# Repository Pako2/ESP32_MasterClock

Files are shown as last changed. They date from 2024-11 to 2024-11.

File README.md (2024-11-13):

# ESP32_MasterClock
## Introduction
The project addresses the solution of a simple source of polarized pulses for slave clock networks. The precise time is obtained from the internet using the NTP protocol. The heart of the device is the **ESP32-C3 SuperMini** module, which connects to the internet via WiFi. A prerequisite for the proper functioning of the device is, of course, an available WiFi signal at the deployment location.
The distribution of pulses is managed by a module equipped with two **A4950** H-bridges. The design of the module was chosen primarily to ensure easy repair in case of failure. The advantage of the dual configuration is that in the event of a failure of one bridge, it should be sufficient to rotate the module and thus use the second, previously unused bridge.
The device does not contain any adjustment elements or a display. All settings are done through a web interface. The status of the device is indicated using two LEDs. The first LED is used to indicate the status of WiFi (via a steady light or blinking). The second LED is a multi-colored (WS2812) and indicates the status of the slave clock using different colors.

Complete project documentation can be found in the [UserGuide_EN.pdf](doc/UserGuide_EN.pdf) file.

## Design of the device
The wiring diagram and circuit board were created using the Eagle design system.
### Wiring diagram
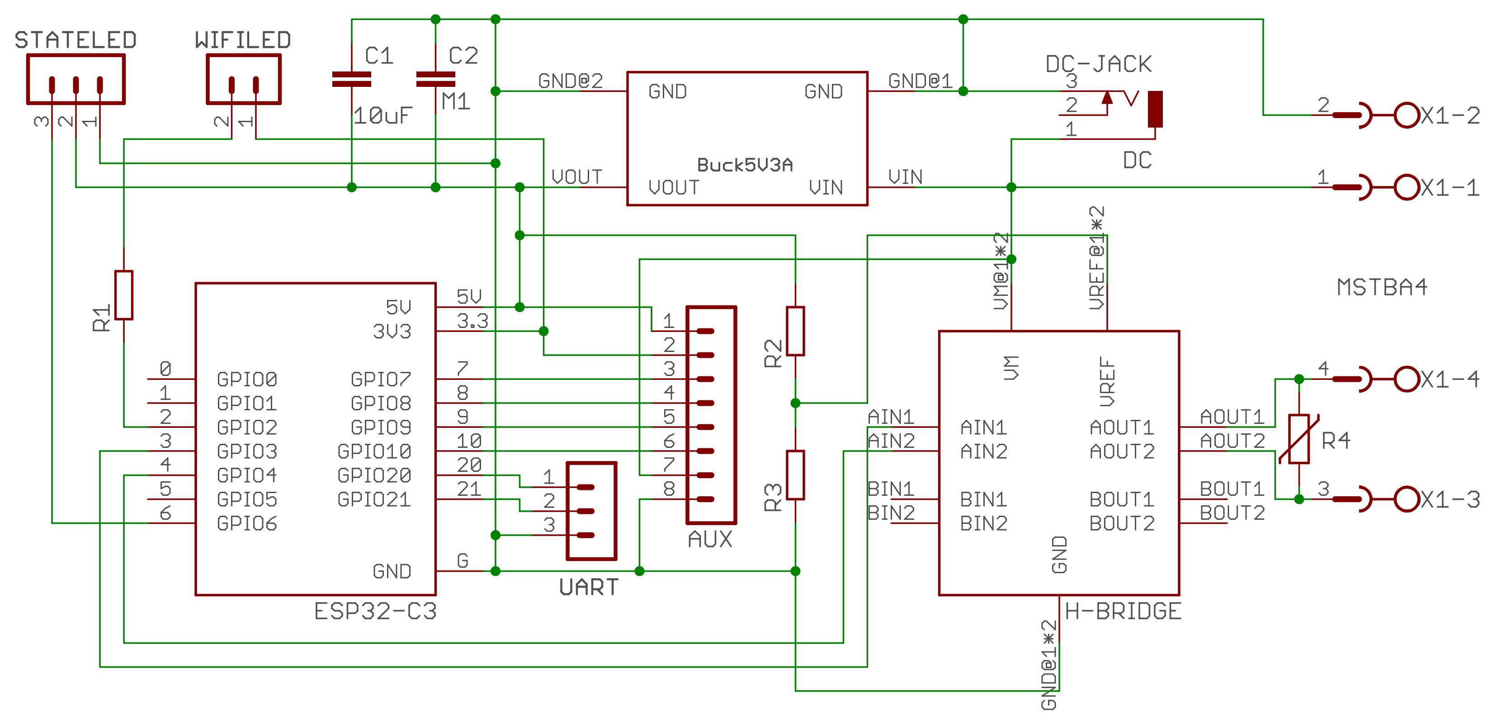
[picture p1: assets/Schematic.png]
Wiring diagram

### Printed circuit board
<p float="left">
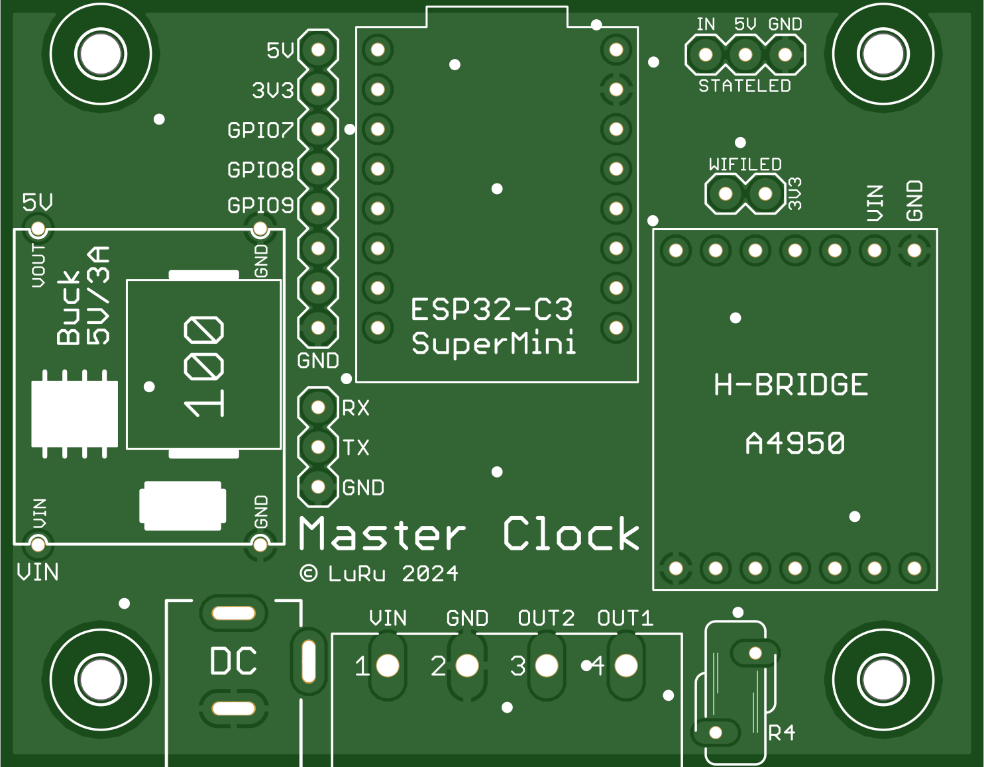
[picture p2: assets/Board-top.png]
PCB top side
  
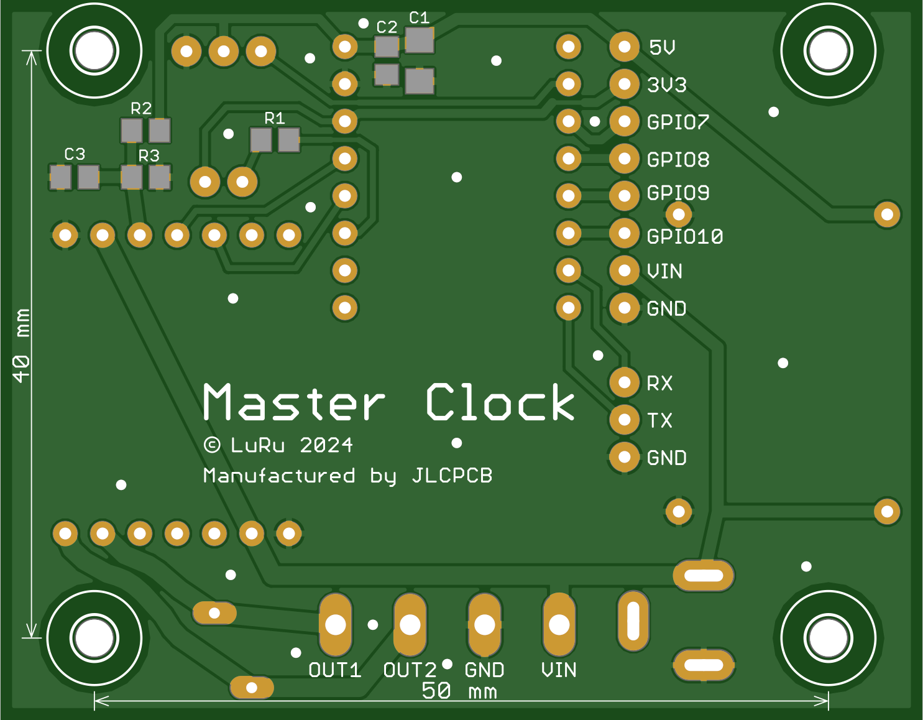
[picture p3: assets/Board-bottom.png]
PCB bottom side
   
</p>

### A box
The size of the printed circuit board and the spacing of the mounting holes were adjusted after the design so that the board fits into some - existing on the market - box. A box with dimensions of 83 x 58 x 33 mm fits perfectly.
<p float="left">
  Open box
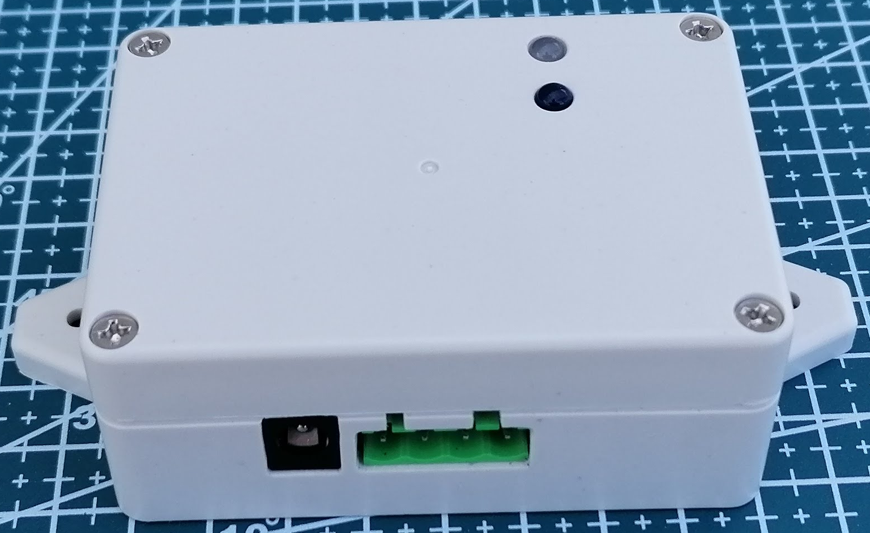
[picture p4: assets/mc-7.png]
Closed box
   
</p>

## Choice of components
Even before the design started, I was clear that one of the ESP32 chips/modules would be used in the device, and it would be one of the many existing modules to ensure easy replacement in case of failure. In the end, I chose one of the smallest modules – **ESP32-C3 SuperMini**. It is small, cheap and more than adequately equipped for the given use.
<p float="left">
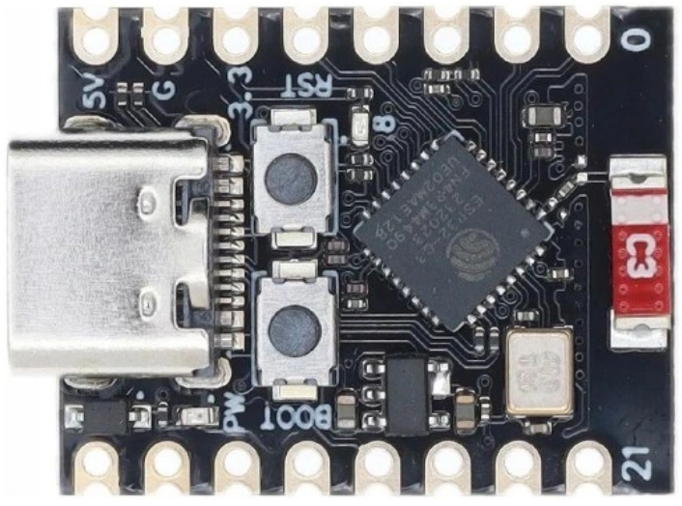
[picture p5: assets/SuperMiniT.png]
SuperMini top side
  
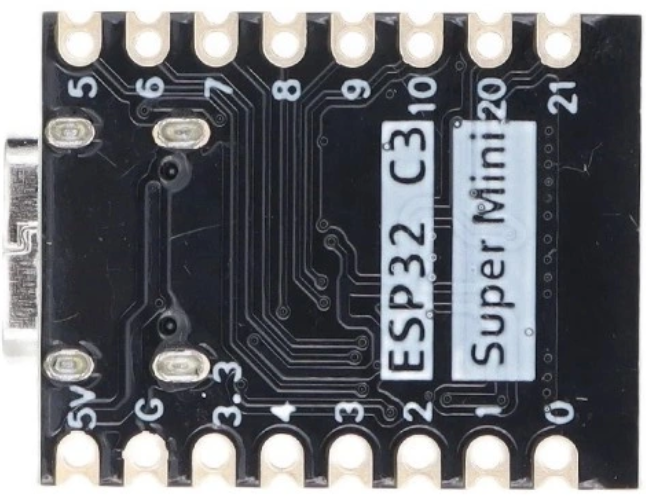
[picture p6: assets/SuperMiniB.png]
SuperMini bottom side
   
</p>

The device is powered by a voltage of 24V, which is required for the correct operation of the slave clock. However, the ESP32-C3 SuperMini module needs a voltage of 5V and therefore a suitable step-down module is used as a power source.
<p float="left">
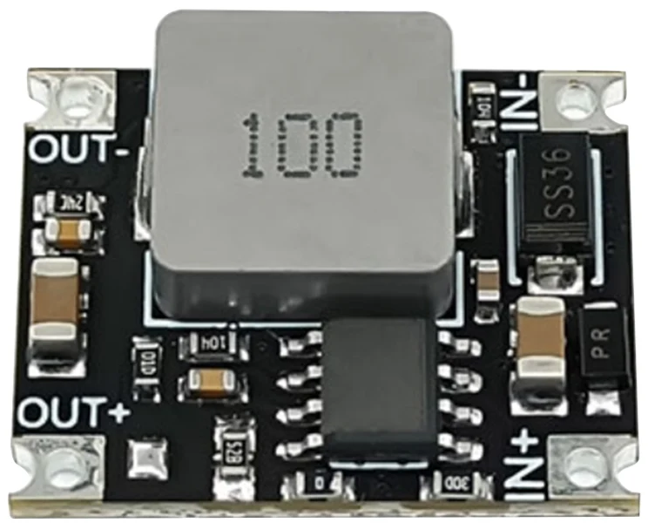
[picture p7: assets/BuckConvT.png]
Step-down converter top side
  
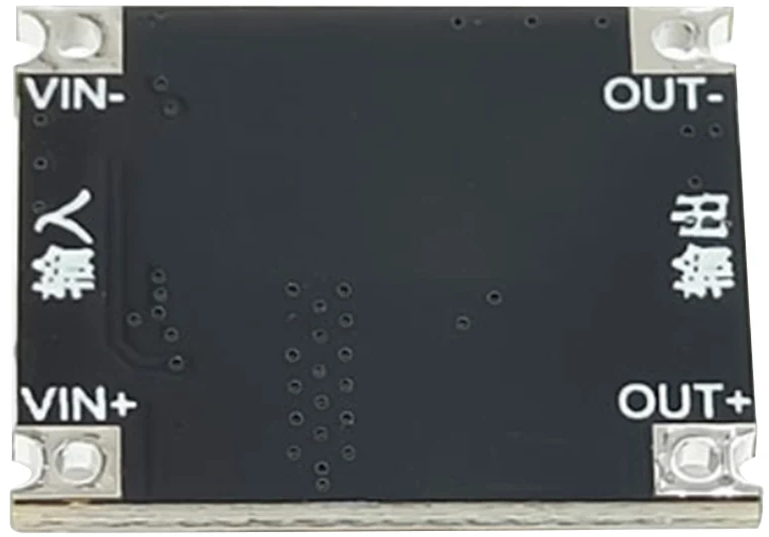
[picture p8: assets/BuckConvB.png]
PStep-down converter bottom side Step-down converter bottom side
   
</p>

The selected converter is sufficiently dimensioned both in terms of input voltage (up to 40V) and output current (up to 3A).

One of the most important components of the entire device is the H-bridge, with which polarized pulses are sent to the slave clocks. For this task, I chose the A4950 module equipped with two bridges, but only one of them is used. The second one can (due to the symmetrical design of the module) be considered as a "spare". In case of failure of the first bridge, it is enough to turn the module by 180°.
<p float="left">
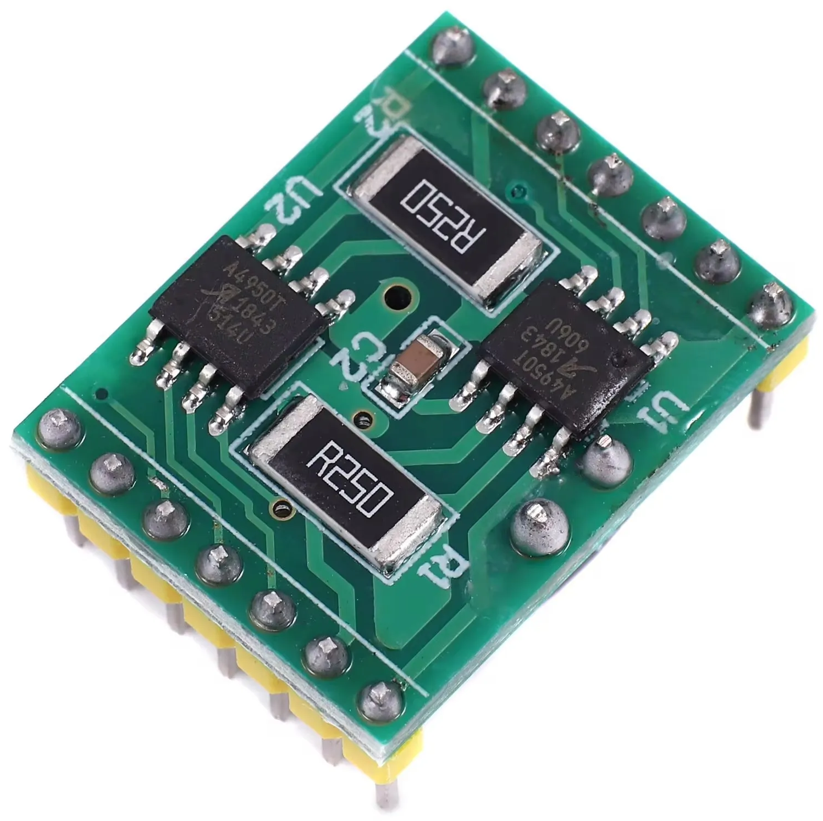
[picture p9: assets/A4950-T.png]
H-bridge top side
  
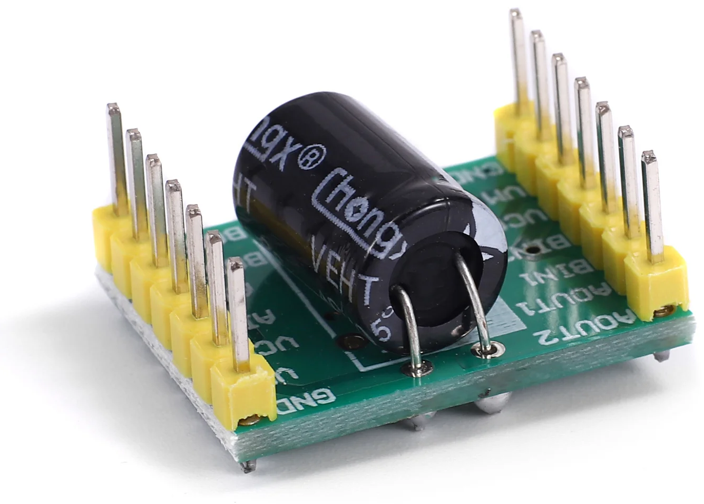
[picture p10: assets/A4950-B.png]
H-bridge bottom side
   
</p>

### Time
The device obtains the exact time from an NTP server. This requires the ESP32 to be connected to the Internet. A possible failure of Internet connectivity only affects the accuracy of the operation, and after the connection is restored, the synchronization with the NTP server (and thus also the accuracy) is automatically restored.
The transition to DST and back is done automatically (thanks to synchronization with the NTP server).
Sometimes it can happen that none of the known WiFi networks are available when the device is turned on (or restarted). Then, of course, it is not possible to synchronize the time with the NTP server. In such an extreme situation, the **Sync Browser Time to Device** button on the **NTP (Time) Settings** page will help.

### License
The code parts written by the author of the **ESP32_MasterClock** project are licensed under [MIT License](LICENSE), 3rd party libraries that are used by this project are licensed under different license schemes, please check them out as well.

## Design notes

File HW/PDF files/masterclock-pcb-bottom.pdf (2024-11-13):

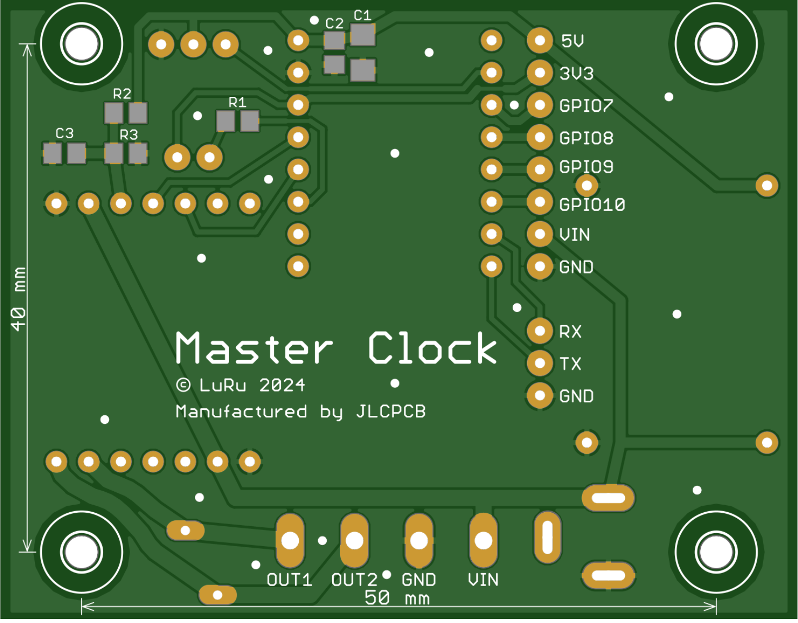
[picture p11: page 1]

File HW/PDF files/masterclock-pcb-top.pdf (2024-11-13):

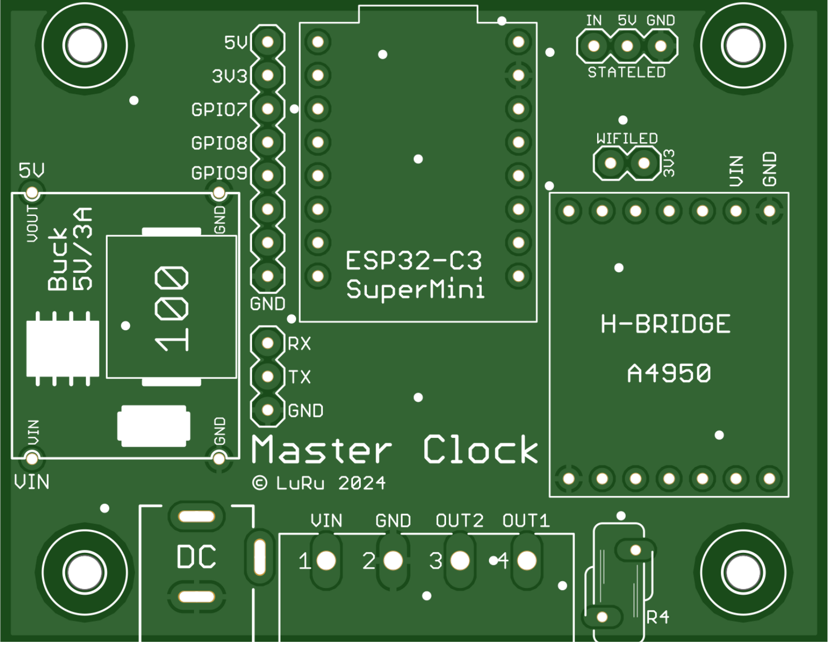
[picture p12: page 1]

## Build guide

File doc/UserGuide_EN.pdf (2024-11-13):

## ESP32_MasterClock

## Introduction

The project deals with the construction of a simple source of polarized pulses for sub-clock networks. The precise time is obtained from the internet using the NTP protocol. The heart of the device is the ESP32-C3 SuperMini module, which connects to the internet via WiFi. A prerequisite for the proper functioning of the device is, of course, an available WiFi signal at the deployment location. A possible failure of Internet connectivity only affects the accuracy of the operation, and after the connection is restored, the synchronization with the NTP server (and thus also the accuracy) is automatically restored.
The transition to DST and back is done automatically (thanks to synchronization with the NTP server).
The distribution of pulses is managed by a module equipped with two A4950 H-bridges. The design of the module was chosen primarily to ensure easy repair in case of failure. The advantage of the dual configuration is that in the event of a failure of one bridge, it should be sufficient to rotate the module and thus use the second, previously unused bridge.
The device does not contain any adjustment elements or a display. All settings are done through a web interface. The status of the device is indicated using two LEDs. The first LED is used to indicate the status of WiFi (via a steady light or blinking). The second LED is a multi-colored (WS2812) and indicates the status of the slave clock using different colors.

## Building With PlatformIO

The build environment is based on VS Code/PlatformIO. The platformio.ini file contains two software variants (data a webh). The data variant is intended primarily for the development phase (but nothing prevents it from being used as a production one), while the webh variant is intended exclusively for production.

The following way of development follows from this:
1) Development takes place exclusively in the software data variant (in the platformio.ini file the line default_envs = webh is commented and the line default_envs = data is uncommented). After editing the source files, the compilation is done in the usual way and the device is upgraded via the serial port.
2) If you also need to edit the *.html or *.js files of the web server, you need to open the
http://< device IP address >/edit page. For this to work, the PC must be connected to the Internet. This is because the online library "ace" (Ajax.org Cloud9 Editor) is used to edit web pages. See https://ace.c9.io/ for more.
3) Once the required functionality is achieved using steps 1 and 2, the webh variant software can be created. This is done by running the Download FS & Create WEBH custom script, accessible through the PROJECT TASKS/data/Custom menu. This will transform the web server files (from the LittleFS file system) into webh files. Maxgerhardt's "pio-esp32-esp8266-filesystem-downloader" utility is used to download the filesystem image and extract it.
4) Switch to the webh variant (in the platformio.ini file, comment out the line default_envs = data and uncomment the line default_envs = webh) and proceed with the compilation. The resulting image „firmware_webh_XXX.bin” (created during the build process) can be found in the directory /bin/webh. The version „XXX“ is set in the platformio.ini file before compilation.

## Upgrade

The device running the webh variant of the firmware can be upgraded very easily through the web interface:
a) In the menu (on the left side of the screen), select the “Update” option.
b) A window will appear showing the current version at the bottom.

c) Use the "Select file" button to search for an update file (e.g. firmware_webh_100.bin) on the computer and start the process with the Update button.
If everything is fine, after restarting the device already contains the new software version.

## First run

When the device is first started, it runs in AP mode by default. On the PC we connect to the "ESP32_MasterClock" network and in the browser to the address 192.168.4.1. A web page with a login dialog should appear. The default password is "admin" (can be changed on the General Settings web page).

## Main menu

After logging in, a welcome screen will appear with basic information about the device. On the left side of the screen is the main menu. Description of main menu items:

Settings
If it is necessary to adjust the device settings (for example, at the first start), we select the Settings item. After clicking on it, the menu will expand and we will see five sub-menus:

Network Settings
On this page, you must first set the network (or multiple networks) to which the device should connect. Press Edit Networks and then New Network. In the dialog window that appears, set the required values. The Scan button can be used to search for available networks. Then you need to press Save Changes. Under the network table, it is possible to change the SSID, IP address and mask (all in AP mode). The changes must be confirmed by pressing the Save button and then also the yellow button with the text You have uncommited changes, please click here to commit and reboot …. However, it is advisable to use this yellow button only after going through all the other settings, because after using it, the device will restart.

Hardware Settings
On this page, it is possible to set the used GPIO pins, the brightness of the status RGB diode and the active level of the WiFi diode (LED, used to display the WiFi status). The set values must be confirmed again by pressing the Save button.
Note: The GPIO for connecting the status (multi-colored) LED must be known at the time of compilation and therefore cannot be changed by the user. It is hardwired to GPIO 6.

General Settings
On this page, it is possible to set the login password (default is "admin") and Host Name. It is confirmed again by pressing the Save button.

NTP (Time) Settings
On this page it is possible to set the NTP server, synchronization interval (in minutes) and time zone. The changes are confirmed again by pressing the Save button.
Sometimes it can happen that none of the known WiFi networks are available when the device is turned on (or restarted). Then, of course, it is not possible to synchronize the time with the NTP server. In such an extreme situation, the Sync Browser Time to Device button will help.

Slave Line Settings
Four parameters are selected on this page:
Line type. Pulse interval 60 or 30 seconds.
Clock cycle. For sub-clocks with an analogue 12-hour dial, but if there are also digital (flip-flop) clocks between the sub-clocks, a 24-hour cycle should normally be used.
Pulse length. It is set according to the type of slave clock.
Gap length. It is used during accelerated catch-up.

The set values must be confirmed again by pressing the Save button.
Slave Line Control
If we select the Slave Line Control item in the menu, we can control the slave line or check its status. After switching on or restarting the device, the slave line is always in the Stopped state. Two clocks are displayed on the page. The first ones show the time of the master clock (should be the correct exact time). The second clock is actually an image of the slave clock and serves to synchronize with its state. We synchronize by setting the time on the clock using the Hour+, Hour-, Min+ and Min- buttons. After execution, we can start the slave line using one of the Start, Wait or Accelerated Catch-Up buttons. Their name corresponds to the function. The Start button doesn't have much practical meaning, but it can come in handy sometimes. The Wait button puts the line in the Waiting state. As soon as the situation arises that the time of the main clock coincides with the time of the slave clock, the device automatically switches the slave line to the Running state. In this state, every full minute (or half-minute in the case of the corresponding type of clock) an impulse is sent to the slave line, which moves it by one step. The Accelerated Catch-Up button will put the line in the state of the same name. The slave clock advances at a rate that is given by the sum of the pulse length and the gap length. As soon as the agreed time with the main clock time is reached, the slave line is switched to the Running state. The meaning of the remaining two buttons is described in the Installation chapter.
Backup & Restore
In the main menu, we can also find the "Backup & Restore" item. The meaning is obvious from the name. It is possible to save a file with a backup of the settings to your PC and easily return to the same settings if necessary. In addition, another function is hidden under the mentioned item - device reboot.
Factory reset
A function of the same name is hidden under this main menu item. After its activation, the configuration file is deleted and after reboot the device is in the same state as when it was first started.
Logout
Použitím tohoto tlačítka se uživatel může odhlásit z webového rozhraní. Je doporučeno provést to vždy po dokončení nastavení či po kontrole stavu podružné linky. Dlouhodobé přihlášení do webového rozhraní zbytečně snižuje spolehlivost zařízení.

## Installation

On the Slave Line Control page we can find two more buttons: Permanent voltage corresponding to an even impulse and Permanent voltage corresponding to an odd impulse. These two buttons are only relevant during system installation. It is used to set the correct polarity of the pulses on all slave clocks. Press one of the listed buttons and check all slave clocks. The corresponding (even or odd) minute (or half minute) should be set on all of them. If this is not the case, we reverse the polarity of the respective clocks. Then, to check, we press the second of the listed buttons and check that the clocks jumped one step to the correct (odd or even) minute (half minute). At the same time, we set all slave clocks to show the same time. We then cancel the permanent voltage by pressing the Stop button and synchronize using the Hour+, Hour-, Min+ and Min- buttons. We complete the installation by pressing the Accelerated Catch-Up or Wait button (at your discretion).

## WiFi LED

The WiFi connection status is indicated by the "WiFi LED". We can distinguish 4 different states:

Connected to one of the set networks
The LED lights up permanently.

Waiting for network after losing connection
Once the connection is lost, the device waits (for an unlimited amount of time) to be restored. The device can connect to any of the set networks. The one with the strongest signal is selected. In the standby state, the diode flashes once. The clock should continue to function during the loss of connection. However, their accuracy is reduced - there is no synchronization with the NTP server.

The device is in user-defined AP mode
If none of the set networks are found after the reset, the device switches to AP mode. If a configuration file exists (the device has been set up at least once), the parameters set on the Network Settings page will be used. In this state, the diode flashes twice.

The device is in default AP mode
At the first startup, after a factory reset, or if a valid configuration file is not found after some problem, the device switches to AP mode using the default parameters (SSID is ESP32_MasterClock and IP address is 192.168.4.1). In this state, the diode flashes three times. A summary of this is in the following table:
WiFi status | LED is on/flashing | Graphic
Connected to the set network | Lights up permanently
Waits for network after connection is lost | Flashes once | ●
AP mode in user settings | Flashes twice | ● ●
AP mode by default | Flashes three times | ● ● ●

## Status LED

The status of the slave line is indicated by a multi-colored LED. The assignment of colors to individual states is in the following table:
Slave line status | LED color
Stopped | Red
Waiting | Purple
Accelerated Catch-Up | Blue
Running | Green
Permanent voltage corresponding to an even impulse | Yellow
Permanent voltage corresponding to an odd impulse | Pink
The same colors indicate line status on the Slave Line Control web page as well.

## Behavior after power failure

Several constructions similar to this can be found on the Internet, and of course there are also professional devices. I noticed that the authors usually deal with the software solution to the power failure problem. The principle of the solution usually consists in the fact that the time of each sent impulse is stored in the EEPROM or other similar memory. When the device starts up after power is restored, the number of missing pulses is calculated from the current time and the time of the last pulse sent. The missing pulses are then sent to the slave line in accelerated mode. The biggest problem with the mentioned solution is obvious – it is the known problem of memory wear. Another error can theoretically also occur if the supply voltage is lost at the time of writing to the memory. It follows that the reliability of the solution is not great. For that reason, I decided not to go down a similar path at all. I personally consider the use of a backed-up source to be a much better solution. It can be either a classic UPS, used in IT technology (especially suitable if there is already a backup source at the installation site) or a special source with a UPS function can be used to power the device. Examples of suitable source types are SCP-35-24 or SCP-50-24 from Mean Well. A huge advantage of this approach is that the clock runs normally even during power outages. It is of course possible that (even though a backup source is used) a power failure will occur. In this case, after power is restored, the slave line will remain in the Stopped state and must be started "manually", i.e. via the Slave Line Control web page.

## Design of the device

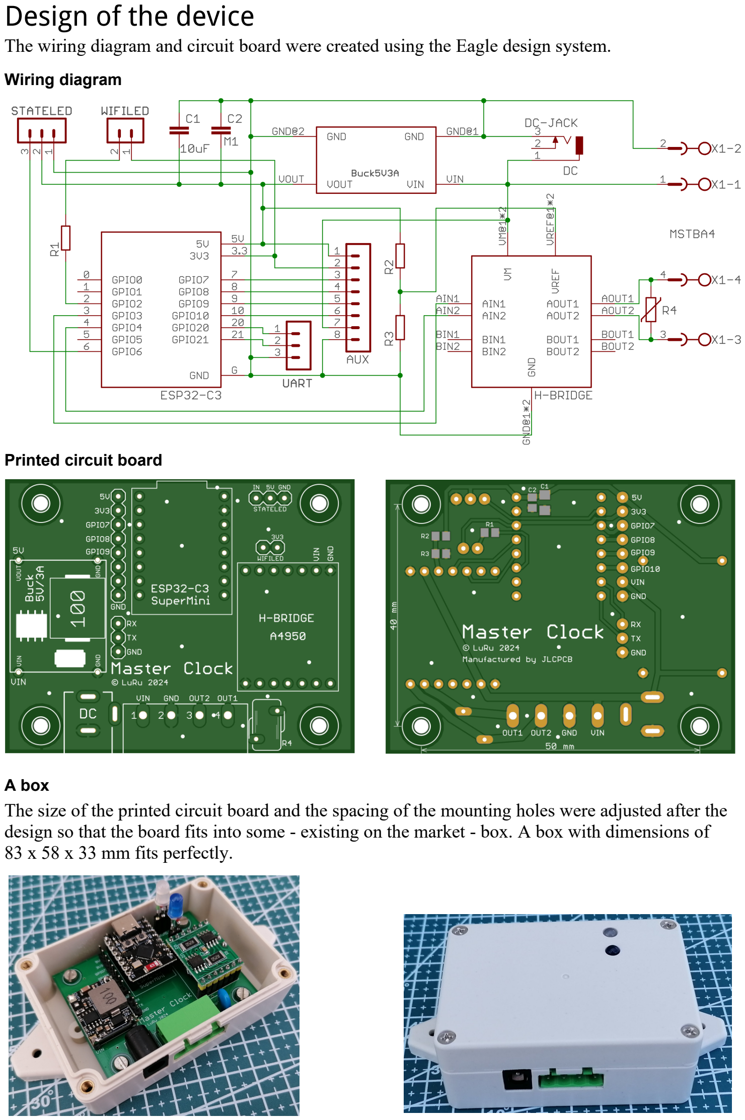
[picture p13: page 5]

The wiring diagram and circuit board were created using the Eagle design system.

Wiring diagram

Printed circuit board

A box
The size of the printed circuit board and the spacing of the mounting holes were adjusted after the design so that the board fits into some - existing on the market - box. A box with dimensions of 83 x 58 x 33 mm fits perfectly.

Choice of components
Even before the design started, I was clear that one of the ESP32 chips would be used in the device, and it would be one of the many existing modules to ensure easy replacement in case of failure. In the end, I chose one of the smallest modules – ESP32-C3 SuperMini. It is small, cheap and more than adequately equipped for the given use.

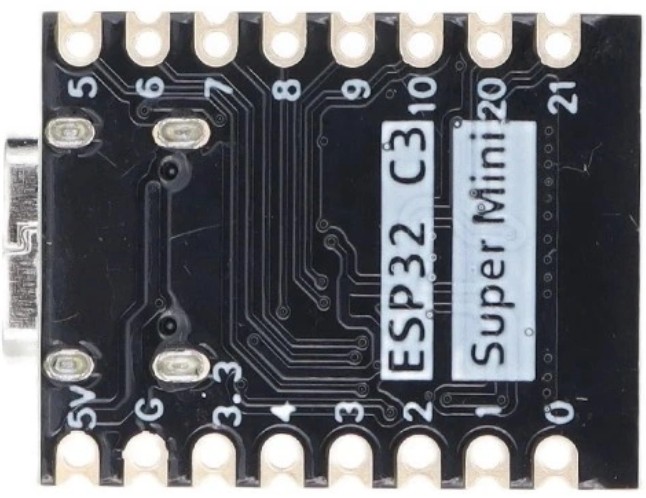
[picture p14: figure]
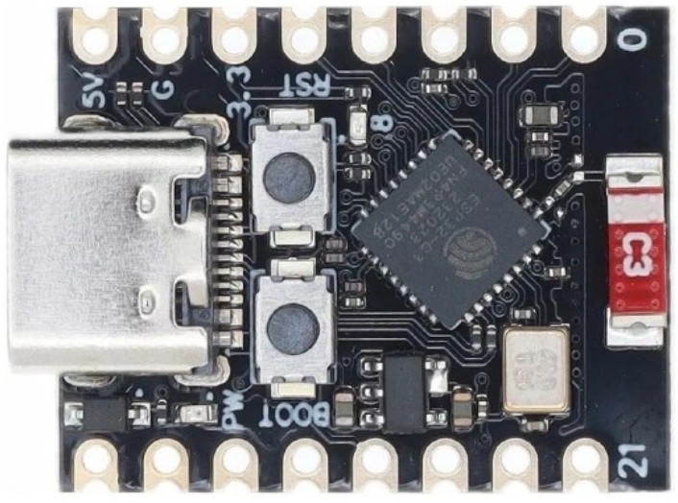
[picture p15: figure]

The device is powered by a voltage of 24V, which is required for the correct operation of the slave clock. However, the ESP32-C3 SuperMini module needs a voltage of 5V and therefore a suitable step-down module is used as a power source.

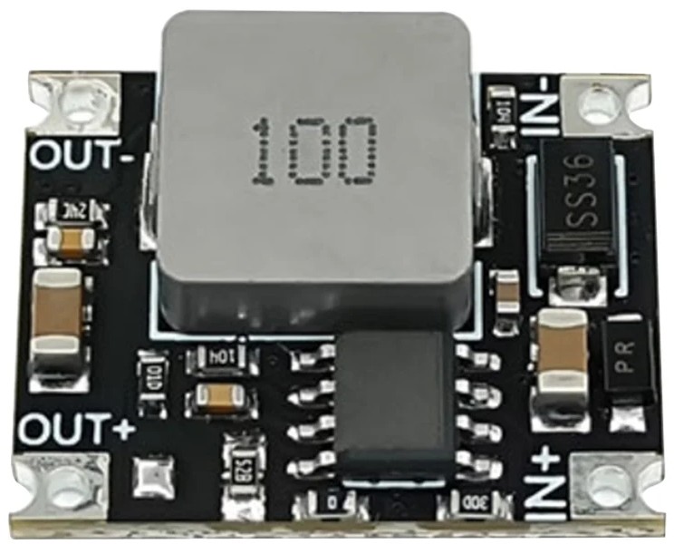
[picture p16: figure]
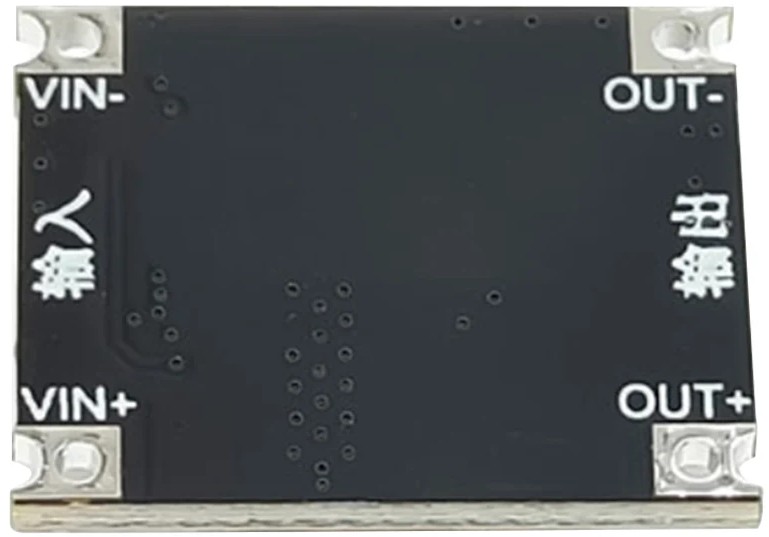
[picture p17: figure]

The selected converter is sufficiently dimensioned both in terms of input voltage (up to 40V) and output current (up to 3A).
One of the most important components of the entire device is the H-bridge, with which polarized pulses are sent to the slave clocks. For this task, I chose the A4950 module equipped with two bridges, but only one of them is used. The second one can (due to the symmetrical design of the module) be considered as a "spare". In case of failure of the first bridge, it is enough to turn the module by 180°.

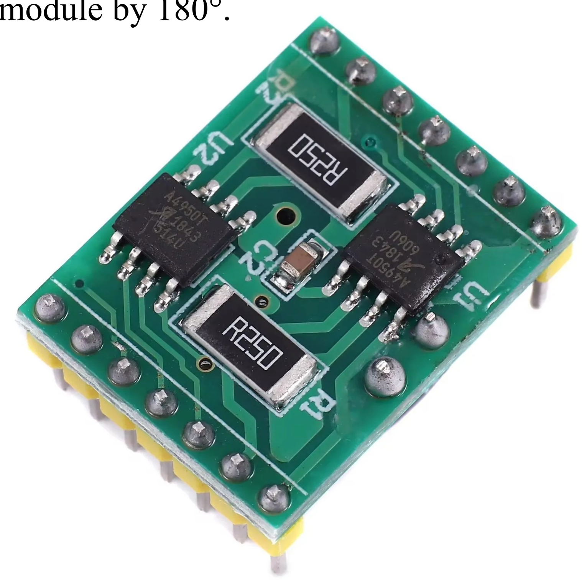
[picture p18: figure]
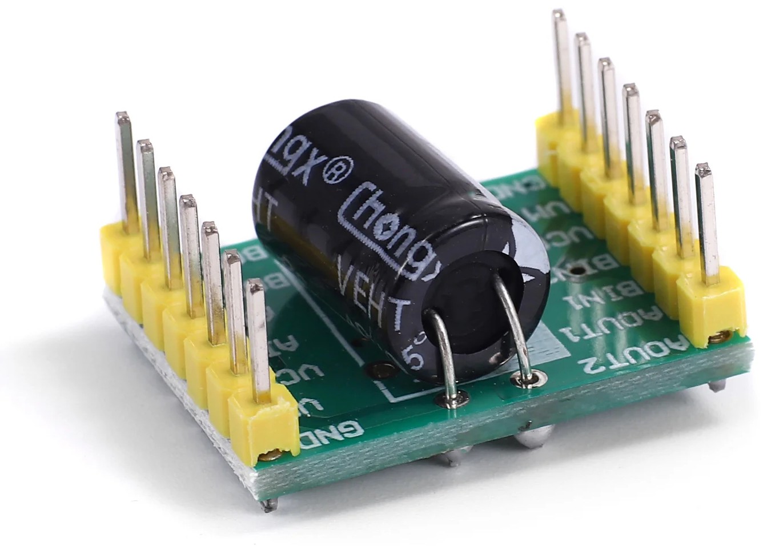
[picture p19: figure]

The rather awkwardly labeled "VCC" inputs are connected to the VREF inputs of both A4950 chips. The VREF input is used to set the current limit. According to the datasheet for the A4950 chip,
IMAX = VREF/(10*Rs), where Rs is the sense resistor. Sensing resistors with a value of 0.25Ω are used on the module. After substitution, the simplified relationship IMAX = VREF * 0.4 comes out. The maximum value of the voltage at the VREF input is 5V, and at this voltage the output current of the bridge is limited to 2A. This is too much for my needs, so I reduced the voltage at the VREF input using a resistor divider, consisting of resistors R2 and R3. It can be deduced that under the given conditions (voltage on the divider 5V and sensing resistor 0.25Ω) the following relationship applies between resistors R2 and R3:

I chose IMAX = 0.5A, so between the resistors R2 and R3, the ratio R2 = R3 * 3 should apply in my case. In the actual design, I used resistors with a resistance of 6.8 kΩ and 2.2 kΩ, which corresponds to IMAX = 0.49A.
Resistor R1 limits the current of the WiFi LED. The choice of its value depends very much on the luminosity of the LED used and on the required light intensity. In any case, resistor R1 should not be less than about 330Ω. Resistor R4 is a 07D390K varistor that serves to protect the A4950 chip. A WS2812 multi-color diode is used as a status diode.
An AUX connector is fitted on the printed circuit board. With its use, it will be possible to expand the device with additional functions in the future. For example, programmable channels for controlling periodic events (like the school bell).
Using the UART connector, it is possible to connect a serial console or, for example, a logger. There is no firmware support for this yet.
The supply voltage can be connected either using the usual "barrel jack" type connector (5.5/2.1mm) or using a screw terminal block, which also has an output of polarized pulses.

R2=R3∗(

2

I MAX

−1)

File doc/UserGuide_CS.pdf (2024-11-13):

## ESP32_MasterClock

## Úvod

Projekt se zabývá konstrukcí jednoduchého zdroje polarizovaných impulsů pro sítě podružných hodin. Přesný čas je získáván z internetu pomocí protokolu NTP. Srdcem zařízení je modul ESP32-C3 SuperMini, který se k internetu připojuje pomocí WiFi. Podmínkou pro správnou funkci zařízení je tedy samozřejmě dostupný WiFi signál v místě nasazení. Případný výpadek internetové konektivity má vliv pouze na přesnost chodu a po obnovení připojení se synchronizace s NTP serverem (a zároveň tedy i přesnost) automaticky obnoví.
Přechod na letní čas a zpět je prováděn automaticky díky synchronizaci s NTP serverem.
K distribuci impulsů slouží modul osazený dvěma H-můstky A4950. Forma modulu byla zvolena zejména z důvodu zajištění možnosti snadné opravy v případě poruchy. Výhodou dvojitého provedení je, že v případě poruchy jednoho můstku by mělo stačit modul otočit a použít tak druhý, doposud nevyužitý můstek.
Zařízení nebsahuje žádné nastavovací prvky a ani displej. Veškerá nastavení se provádějí přes webové rozhraní. Stav zařízení je indikován pomocí dvou LED diod. První LED je určena pro indikaci stavu WiFi (pomocí trvalého svitu anebo blikání). Druhá LED je vícebarevná (WS2812) a pomocí různých barev indikuje stav podružné linky.

## Vývoj s VS Code a PlatformIO

Vývojové prostředí je založeno na VS Code/PlatformIO. Soubor platformio.ini obsahuje dvě varianty software (data a webh). Varianta data je určena především pro fázi vývoje (ale nic nebrání používat to i jako produkční), zatímco varianta webh je zamýšlena výhradně jako produkční.

Z toho vyplývá následující způsob vývoje:
1) Vývoj probíhá výhradně ve variantě software data (v platformio.ini souboru je zakomentován řádek default_envs = webh a odkomentován řádek default_envs = data) . Po úpravě zdrojových souborů se obvyklým způsobem provede kompilace a zařízení se upgraduje přes sériový port.
2) Pokud je nutné upravit i soubory *.html nebo *.js webového serveru, je třeba otevřít stránku http://< IP adresa za řízení>/edit. Aby to fungovalo, PC musí být připojen na internet. K editování je totiž využívána online knihovna „ace“ (Ajax.org Cloud9 Editor). Více viz https://ace.c9.io/.
3) Jakmile se pomocí kroků 1 a 2 dosáhne požadované funkcionality, lze vytvořit webh variantu software. To se provede spuštěním uživatelského skriptu Download FS & Create WEBH, který je dostupný prostřednictvím nabídky PROJECT TASKS/data/Custom. Tím dojde k transformaci souborů webového serveru (ze souborového systému LittleFS) do souborů webh. Ke stažení obrazu souborového systému a jeho extrakci je použita utilita „pio-esp32-esp8266-filesystem-downloader“ od maxgerhardt.
4) Přepnout na variantu webh (v platformio.ini souboru zakomentovat řádek default_envs = data a odkomentovat řádek default_envs = webh) a provést kompilaci. Výsledný obraz „firmware_webh_XXX.bin” (vytvořený během procesu kompilace) lze nalézt v adresáři /bin/webh. Verze „XXX“ se nastavuje v souboru platformio.ini před kompilací.

## Upgrade

Zařízení, ve kterém běží webh varianta firmware, může být upgradováno velmi snadno prostřednictvím webového rozhraní:
a) V nabídce (na levé straně obrazovky) vybereme položku „Update“.
b) Objeví se okno, které v dolní části zobrazuje aktuální verzi.
c) Pomocí tlačítka „Vybrat soubor“ lze v počítači vyhledat soubor s updatem (např. firmware_webh_100.bin) a tlačítkem Update proces spustit.

Pokud je vše v pořádku, po restartu již zařízení obsahuje novou verzi software.

## První spuštění

Jakmile je zařízení poprvé spuštěno, běží ve výchozím nastavení v režimu AP. Na PC se připojíme k síti „ESP32_MasterClock“ a v prohlížeči na adresu 192.168.4.1. Měla by se objevit webová stránka s přihlašovacím dialogem. Výchozí heslo je „admin“ (lze změnit na webové stránce General Settings).

## Hlavní nabídka

Po přihlášení se objeví uvítací obrazovka se základními údaji o zařízení. V levé části obrazovky je hlavní nabídka. Popis položek hlavní nabídky:

Settings
Je-li třeba upravit nastavení zařízení (například při prvním spuštění), vybereme položku „Settings“. Po kliknutí na ni se nabídka rozbalí a uvidíme pět dílčích nabídek:

Network Settings
Na této stránce je třeba nastavit zejména síť (případně více sítí), na kterou se má zařízení připojit. Stiskneme Edit Networks a následně New Network. V dialogovém okně, které se objeví nastavíme požadované hodnoty. Lze použít tlačítko Scan k vyhledání dostupných sítí. Po nastavení stiskneme Save Changes. Pod tabulkou sítí je možné ještě změnit SSID, IP adresu a masku (vše v AP režimu). Změny je třeba potvrdit stisknutím tlačítka Save a posléze také žlutého tlačítka s textem You have uncommited changes, please click here to commit and reboot …. Toto žluté tlačítko je však vhodné použít teprve až po projití všech ostatních nastavení, protože po jeho použití se zařízení restartuje.

Hardware Settings
Na této stránce je možné nastavit použité GPIO piny, jas stavové RGB diody a aktivní úroveň WiFi diody (LED, použitá k zobrazení stavu WiFi). Nastavené hodnoty je opět třeba potvrdit stisknutím tlačítka Save.
Poznámka: | GPIO pro připojení stavové (vícebarevné) LED musí být znám už v době kompilace
| a proto ho není možné uživatelsky měnit. Je napevno určeno GPIO 6.

General Settings
Na této stránce je možné nastavit přihlašovací heslo (výchozí je „admin“) a Host Name. Potvrzuje se opět stisknutím tlačítka Save.

NTP (Time) Settings
Na této stránce je možné nastavit NTP server, interval synchronizace (v minutách) a časovou zónu. Změny se opět potvrzují stisknutím tlačítka Save.
Někdy se může stát, že v době zapnutí (nebo restartu) zařízení není dostupná žádná ze známých WiFi sítí. Potom samozřejmě není možné synchronizovat čas s NTP serverem. V takové krajní situaci pomůže tlačítko Sync Browser Time to Device.

Slave Line Settings
Na této stránce se volí čtyři parametry:
Typ linky. Interval impulsu 60 nebo 30 sekund.
Hodinový cyklus. Pro podružné hodiny s analogovým ciferníkem 12 hodin, ale jsou-li mezi podružnými hodinami i digitální (překlápěcí) hodiny, je třeba obvykle použít cyklus 24 hodin. Délka impulsu. Nastavuje se podle typu podružných hodin.
Délka mezery. Použije se při zrychleném doběhu.
Nastavené hodnoty je opět třeba potvrdit stisknutím tlačítka Save.

Slave Line Control
Vybereme-li v nabídce položku Slave Line Control, můžeme ovládat podružnou linku anebo kontrolovat její stav. Po zapnutí anebo restartu zařízení je podružná linka vždy ve stavu Stopped. Na stránce jsou zobrazeny dvoje hodiny. První ukazují čas hlavních hodin (měl by to být správný přesný čas). Druhé hodiny jsou vlastně obrazem podružných hodin a slouží k synchronizaci s jejich stavem. Synchronizaci provedeme tak, že na hodinách nastavíme čas pomocí tlačítek Hour+, Hour-, Min+ a Min-. Po provedení můžeme podružnou linku spustit pomocí některého z tlačítek Start, Wait nebo Accelerated Catch-Up. Jejich název odpovídá funkci. Tlačítko Start nemá moc praktický význam, ale někdy se může hodit. Tlačítko Wait uvede linku do stavu Waiting. Jakmile nastane situace, že čas hlavních hodin se shoduje s časem podružných hodin, zařízení automaticky přepne podružnou linku do stavu Running. V tomto stavu pak v každou celou minutu (nebo půlminutu v případě odpovídajícího typu hodin) je do podružné linky odeslán impuls, který je o krok posune. Tlačítko Accelerated Catch-Up uvede linku do stejnojmenného stavu. Podružné hodiny se posunují rychlostí, která je dána součtem délky impulsu a délky mezery. Jakmile se dosáhne souhlasného času s časem hlavních hodin, podružná linka je přepnuta do stavu Running. Význam zbylých dvou tlačítek je popsán v kapitole „Instalace“.

Backup & Restore
V hlavní nabídce dále nalezneme položku „Backup & Restore“. Význam je zřejmý z názvu. Je možné uložit si do PC soubor se zálohou nastavení a v případě potřeby se ke stejnému nastavení snadno vrátit. Pod uvedenou položkou se navíc skrývá i další funkce – reboot zařízení.

Factory reset
Pod touto položkou hlavní nabídky se skrývá stejnojmenná funkce. Po její aktivaci se vymaže konfigurační soubor a po rebootu je zařízení ve stejném stavu jako při prvním spuštění.

Logout
Použitím tohoto tlačítka se uživatel může odhlásit z webového rozhraní. Je doporučeno provést to vždy po dokončení nastavení či po kontrole stavu podružné linky. Dlouhodobé přihlášení do webového rozhraní zbytečně snižuje spolehlivost zařízení.

## Instalace

Na stránce Slave Line Control můžeme najít ještě dvě tlačítka: Permanent voltage corresponding to an even impulse a Permanent voltage corresponding to an odd impulse. Tato dvě tlačítka mají význam jen v době instalace systému. Slouží k tomu, aby na všech podružných hodinách byla nastavena správná polarita impulsů. Stiskneme jedno z uvedených tlačítek a zkontrolujeme všechny podružné hodiny. Na všech by měla být nastavena odpovídající (sudá nebo lichá) minuta (či půlminuta). Pokud to tak není, u příslušných hodin otočíme polaritu. Potom pro kontrolu stiskneme druhé z uvedených tlačítek a zkontrolujeme, že hodiny poskočily o jeden krok na správnou (lichou či sudou) minutu (půlminutu). Zároveň nastavíme všechny podružné hodiny tak, aby ukazovaly shodný čas. Trvalé napětí pak zrušíme stiskem tlačítka Stop a pomocí tlačítek Hour+, Hour-, Min+ a Min- provedeme synchronizaci. Instalaci dokončíme stiskem tlačítka Accelerated Catch-Up nebo Wait (podle uvážení).

## WiFi LED

Stav připojení k WiFi je signalizován diodou „WiFi LED“. Můžeme rozeznat 4 různé stavy:

Připojeno k některé z nastavených sítí
Dioda svítí trvale.

Čekání na síť po ztrátě spojení
Jakmile dojde ke ztrátě spojení, zařízení čeká (neomezeně dlouhou dobu) na obnovení. Zařízení se může připojit na kteroukoliv z nastavených sítí. Vybere se ta, která má nejsilnější signál. Ve stavu čekání dioda bliká jednou. Během ztráty spojení by hodiny měly i nadále fungovat. Jejich přesnost je však snížena – nedochází k synchronizaci s NTP serverem.

Zařízení je v uživatelsky nastaveném režimu AP
Jestliže po resetu není nalezena žádná z nastavených sítí, zařízení se přepne do režimu AP. Pokud existuje konfigurační soubor (zařízení bylo alespoň jednou nastaveno), použijí se parametry, nastavené na stránce Network Settings. V tomto stavu dioda bliká dvakrát.

Zařízení je ve výchozím AP režimu
Při prvním spuštění, po továrním resetu anebo v případě že po nějakém problému není nalezen platný konfigurační soubor, zařízení se přepne do režimu AP s využitím výchozích parametrů (SSID je ESP32_MasterClock a IP adresa je 192.168.4.1).V tomto stavu dioda bliká třikrát. Shrnutí uvedeného je v následující tabulce:
Stav WiFi | LED svítí/bliká | Graficky
Připojeno k nastavené síti | Svítí trvale
Čeká na síť po ztrátě spojení | Bliká jednou | ●
AP režim v uživatelském nastavení | Bliká dvakrát | ● ●
AP režim ve výchozím nastavení | Bliká třikrát | ● ● ●

## Stavová LED

Stav podružné linky je indikován vícebarevnou LED diodou. Přiřazení barev k jednotlivým stavům je v následující tabulce:
Stav podružné linky | Barva diody
Zastavena | Červená
Čekající | Fialová
Accelerated Catch-Up | Modrá
Běžící | Zelená
Permanent voltage corresponding to an even impulse | Žlutá
Permanent voltage corresponding to an odd impulse | Růžová
Stejné barvy indikují stav linky také na webové stránce Slave Line Control.

## Chování po výpadku napájení

Na internetu lze nalézt několik konstrukcí, podobných této a existují samozřejmě i profesionální zařízení. Všimnul jsem si, že autoři se obvykle zabývají softwarovým řešením problému výpadku napájení. Princip řešení většinou spočívá v tom, že do EEPROM nebo jiné podobné paměti je ukládán čas každého odeslaného impulsu. Jakmile se zařízení spustí po obnovení napájení,
z aktuálního času a času posledního odeslaného impulsu je vypočten počet chybějících impulsů. Chybějící impulsy jsou pak ve zrychleném režimu odeslány do podružné linky. Největší problém uvedeného řešení je zřejmý – je to známý problém opotřebení paměti. Další chyba může teoreticky nastat i v případě, že ke ztrátě napájecího napětí dojde v okamžiku zápisu do paměti. Z toho vyplývá, že spolehlivost řešení není nijak velká. Z toho důvodu jsem se rozhodl obdobnou cestou vůbec nejít. Za daleko lepší řešení osobně považuji použití zálohovaného zdroje. Může to být buď klasická UPS, používaná v IT technice (vhodné zejména v případě, že v místě instalace už nějaký záložní zdroj existuje) anebo se k napájení zařízení může použít speciální zdroj s funkcí UPS. Příkladem vhodných typů zdrojů jsou SCP-35-24 anebo SCP-50-24 od firmy Mean Well. Obrovskou výhodou tohoto přístupu je to, že hodiny normálně jdou i během přerušení dodávky elektrické energie.
Je samozřejmě možné, že (přestože je použit zálohovaný zdroj) k výpadku napájení dojde.

## Konstrukce zařízení

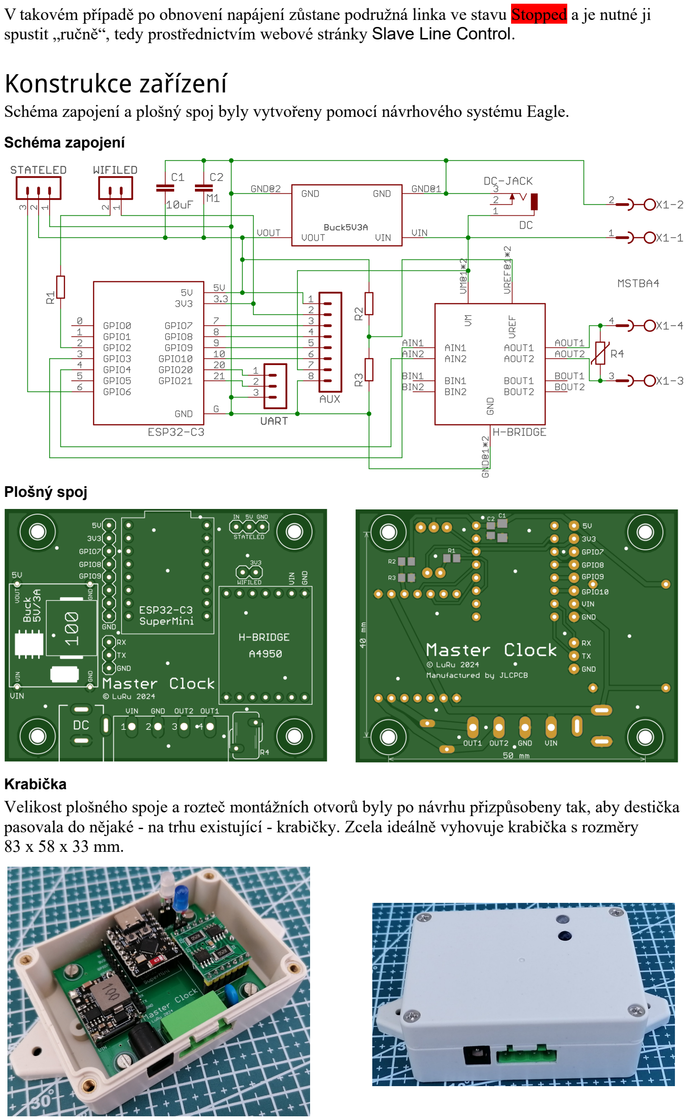
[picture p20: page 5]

V takovém případě po obnovení napájení zůstane podružná linka ve stavu Stopped a je nutné ji spustit „ručně“, tedy prostřednictvím webové stránky Slave Line Control.

Schéma zapojení a plošný spoj byly vytvořeny pomocí návrhového systému Eagle.

Schéma zapojení

Plošný spoj

Krabička
Velikost plošného spoje a rozteč montážních otvorů byly po návrhu přizpůsobeny tak, aby destička pasovala do nějaké - na trhu existující - krabičky. Zcela ideálně vyhovuje krabička s rozměry
83 x 58 x 33 mm.

Volba součástek
Již před začátkem návrhu jsem měl jasno v tom, že v zařízení bude použit některý z čipů ESP32
a pro zajištění možnosti jednoduché výměny v případě poruchy to bude některý z mnoha existujících modulů. Nakonec jsem vybral jeden z nejmenších modulů – ESP32-C3 SuperMini. Je malý, levný a pro dané použití více než dostatečně vybavený.


Zařízení je napájeno napětím 24V, které je potřeba pro správnou funkci podružných hodin. Modul ESP32-C3 SuperMini však potřebuje napětí 5V a proto je jako napájecí zdroj použit vhodný step-down modul.


Vybraný převodník je dostatečně dimenzovaný jak z hlediska vstupního napětí (až 40V), tak výstupního proudu (až 3A).
Jednou z nejdůležitějších komponent celého zařízení je H-můstek, pomocí kterého jsou do podružných hodin posílány polarizované impulsy. Pro tento úkol jsem vybral modul A4950 osazný dvěma můstky, z nichž využit je ale jen jeden. Druhý je možné (vzhledem k symetrické konstrukci modulu) považovat za „náhradní“. V případě poruchy prvního můstku stačí modul otočit o 180°.

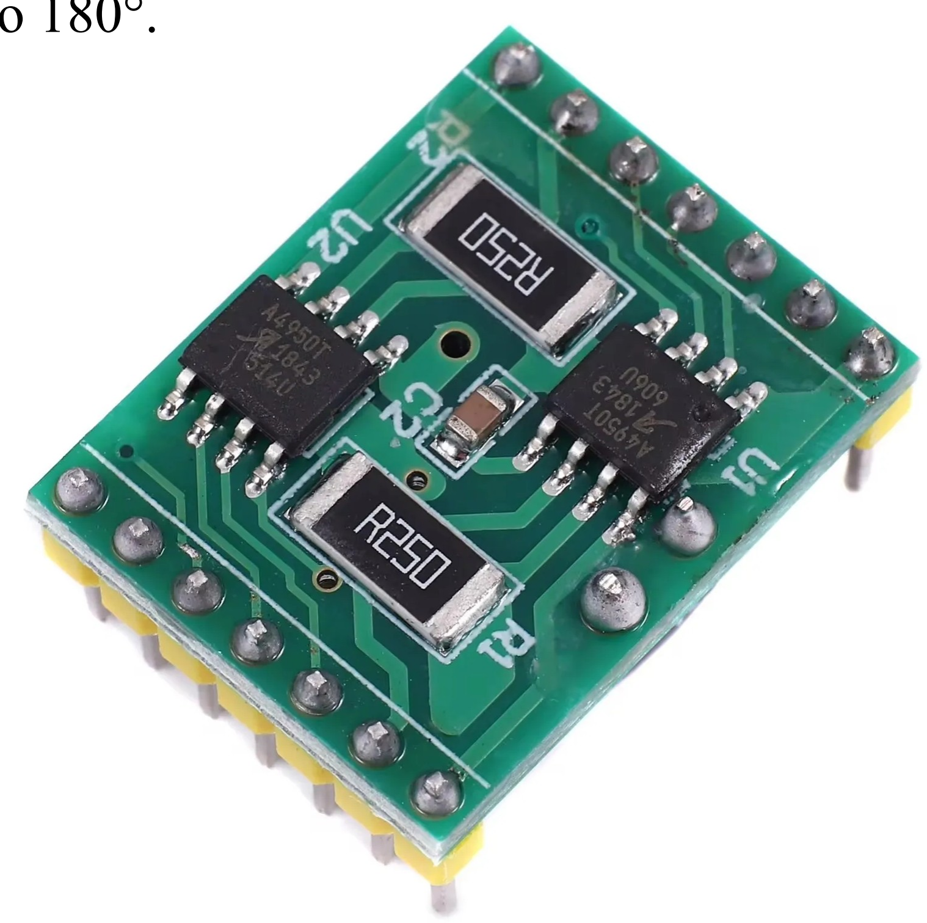
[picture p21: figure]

Poměrně nevhodně označené vstupy „VCC“ jsou připojeny na vstupy VREF obou čipů A4950. Vstup VREF slouží k nastavení proudového omezení. Podle datasheetu k čipu A4950 platí, že IMAX = VREF/(10*Rs), kde Rs je snímací rezistor. Na modulu jsou použity snímací rezistory
s hodnotou 0.25Ω. Po dosazení vyjde zjednodušený vztah IMAX = VREF * 0.4. Maximální hodnota napětí na vstupu VREF je 5V a při tomto napětí je výstupní proud můstku omezen na 2A. To je pro moje potřeby zbytečně mnoho a tak jsem napětí na vstupu VREF snížil pomocí odporového děliče, složeného z rezistorů R2 a R3. Lze odvodit, že při daných podmínkách (napětí na děliči 5V
a snímací rezistor 0.25Ω) platí mezi rezistory R2 a R3 tento vztah:

Zvolil jsem IMAX = 0.5A, takže mezi rezistory R2 a R3 by měl v mém případě platit poměr
R2 = R3 * 3. Ve skutečném provedení jsem použil rezistory s odporem 6.8 kΩ a 2.2 kΩ, což odpovídá IMAX = 0.49A.
Rezistor R1 omezuje proud LED diodou WIFILED. Volba jeho hodnoty velice záleží na svítivosti použité LED diody a na požadované intenzitě světla. V každém případě by rezistor R1 neměl být menší než asi 330Ω. Rezistor R4 je varistor 07D390K, který slouží k ochraně čipu A4950.
Jako stavová dioda je použita vícebarevná dioda typu WS2812.
Na desce plošných spojů je osazen konektor AUX. S jeho využitím bude možné v budoucnu přístroj rozšířit o další funkce. Například programovatelné kanály pro ovládání pravidelných událostí (jako je školní zvonek).
Pomocí UART konektoru je možné připojit sériovou konzoli nebo např. logger. Pro to zatím není podpora ve firmware.
Napájecí napětí je možné připojit buď pomocí obvyklého konektoru typu „barel jack“ (5,5/2,1mm) anebo pomocí šroubovací svorkovnice, na které je i výstup polarizovaných impulsů.

R2=R3∗(

2

I MAX

−1)

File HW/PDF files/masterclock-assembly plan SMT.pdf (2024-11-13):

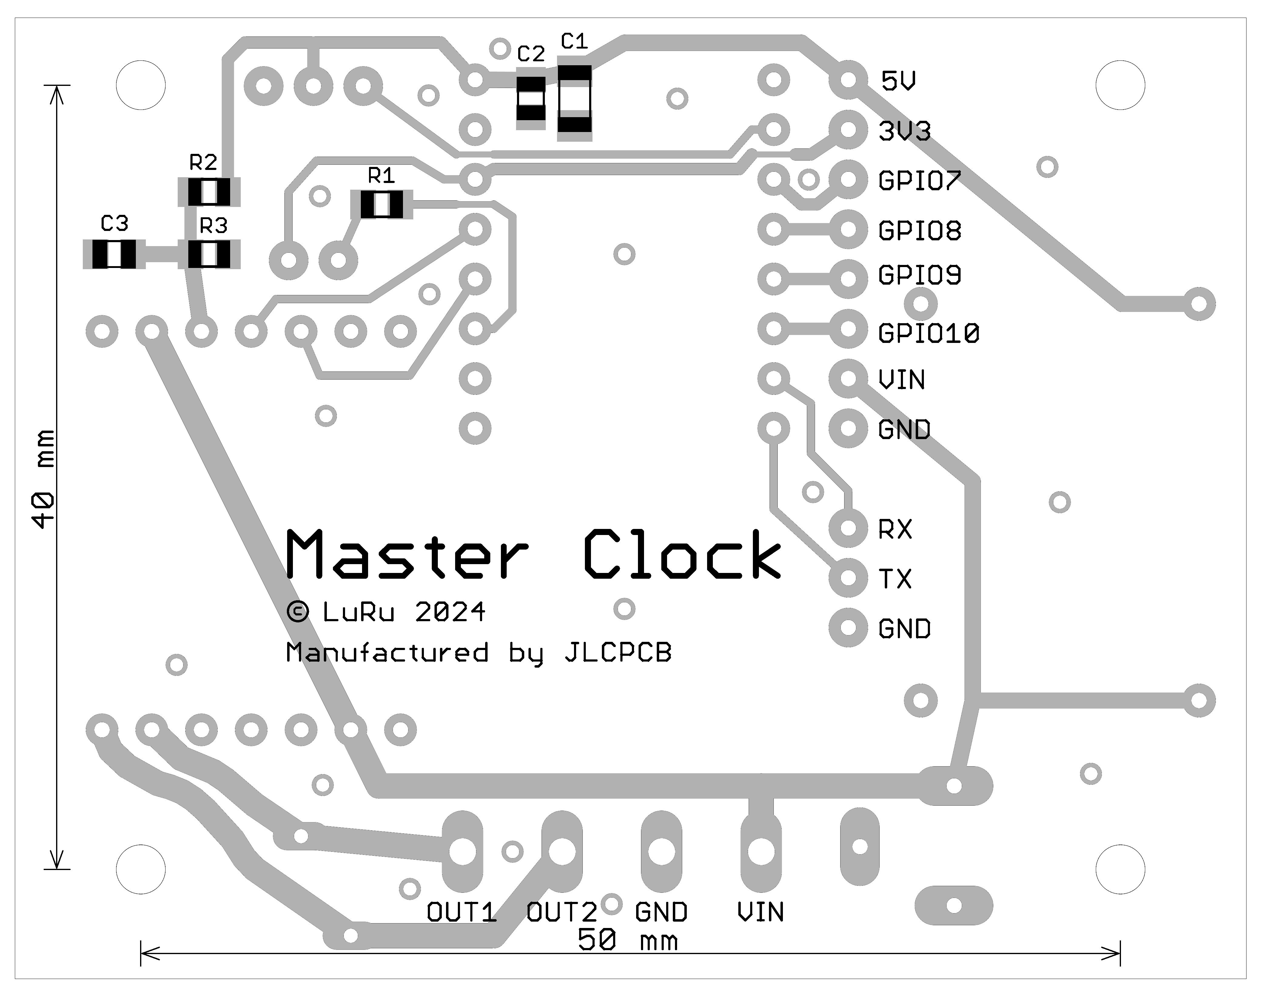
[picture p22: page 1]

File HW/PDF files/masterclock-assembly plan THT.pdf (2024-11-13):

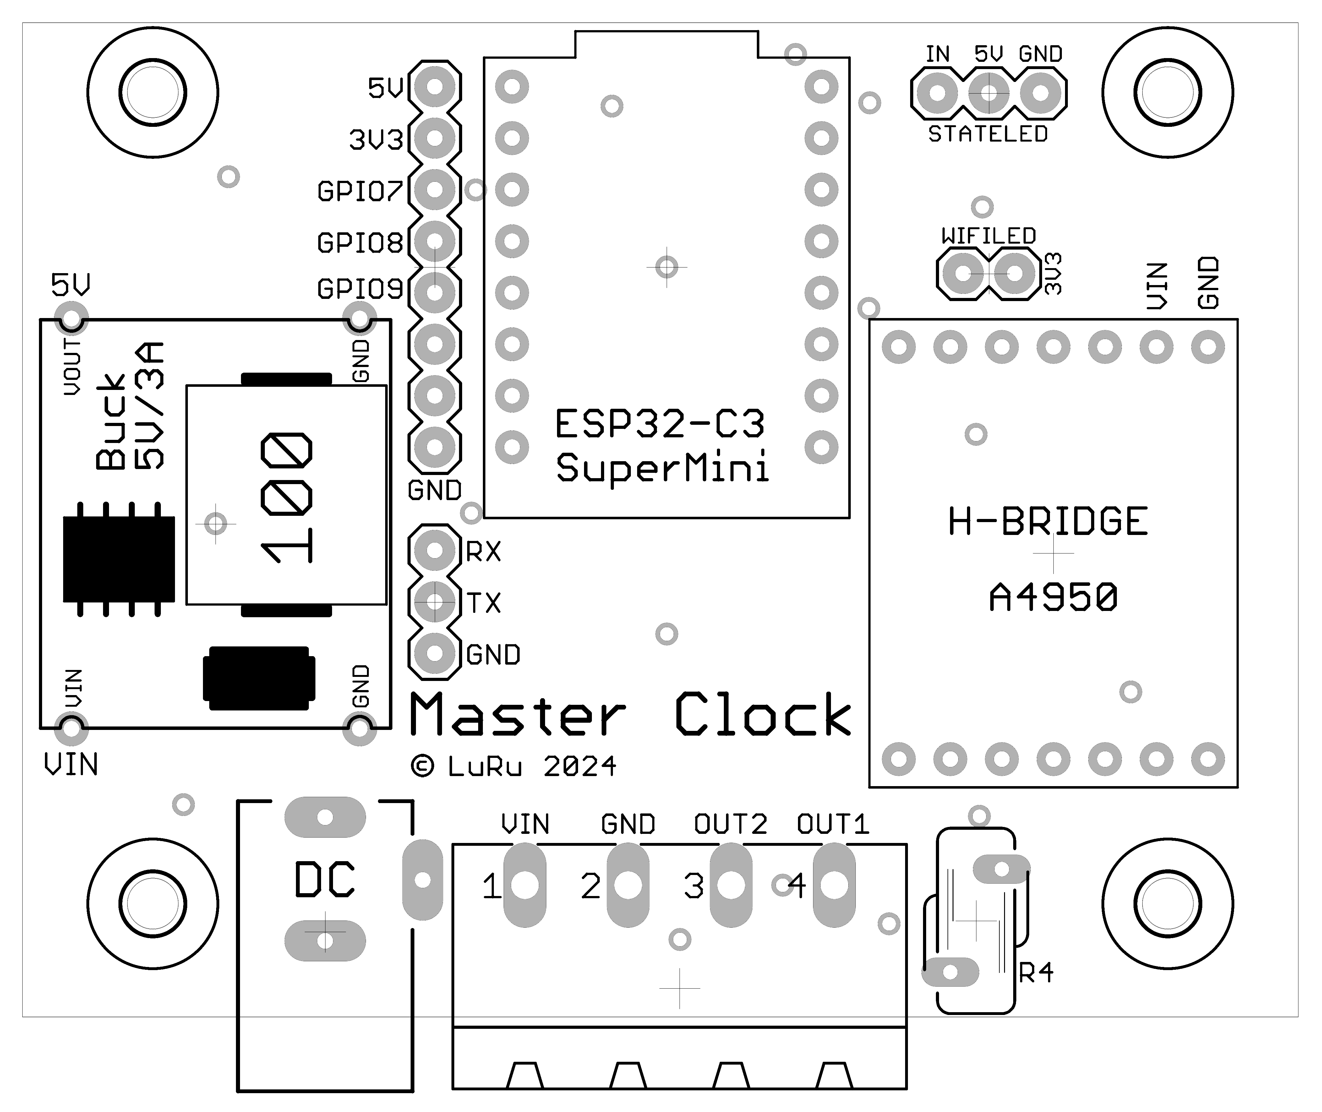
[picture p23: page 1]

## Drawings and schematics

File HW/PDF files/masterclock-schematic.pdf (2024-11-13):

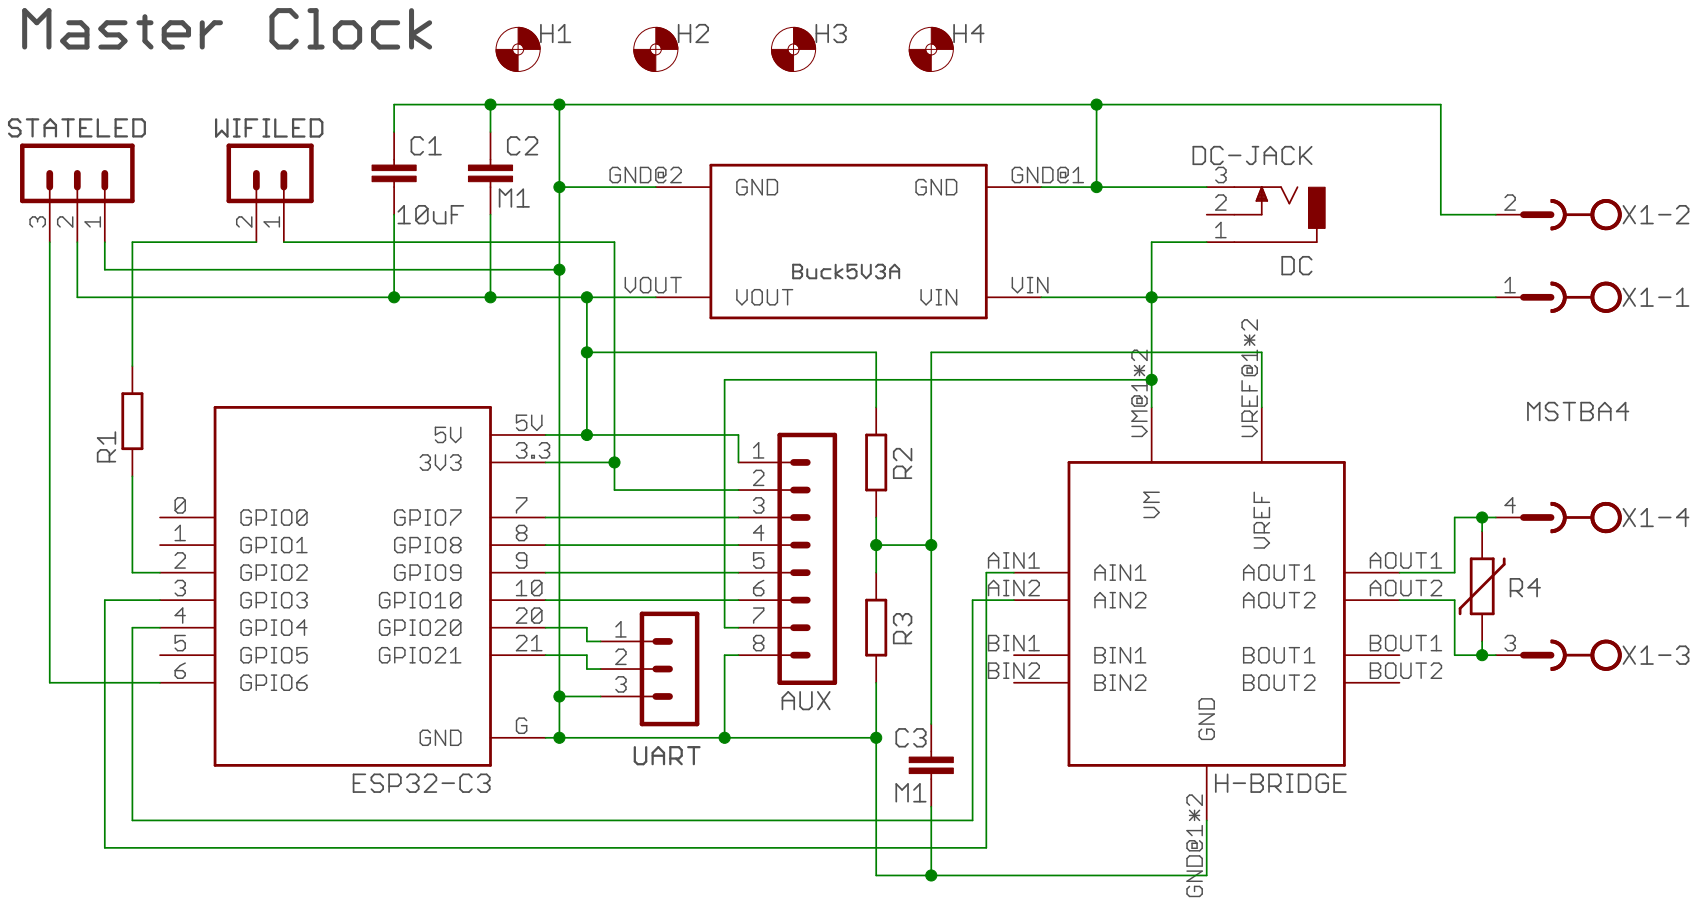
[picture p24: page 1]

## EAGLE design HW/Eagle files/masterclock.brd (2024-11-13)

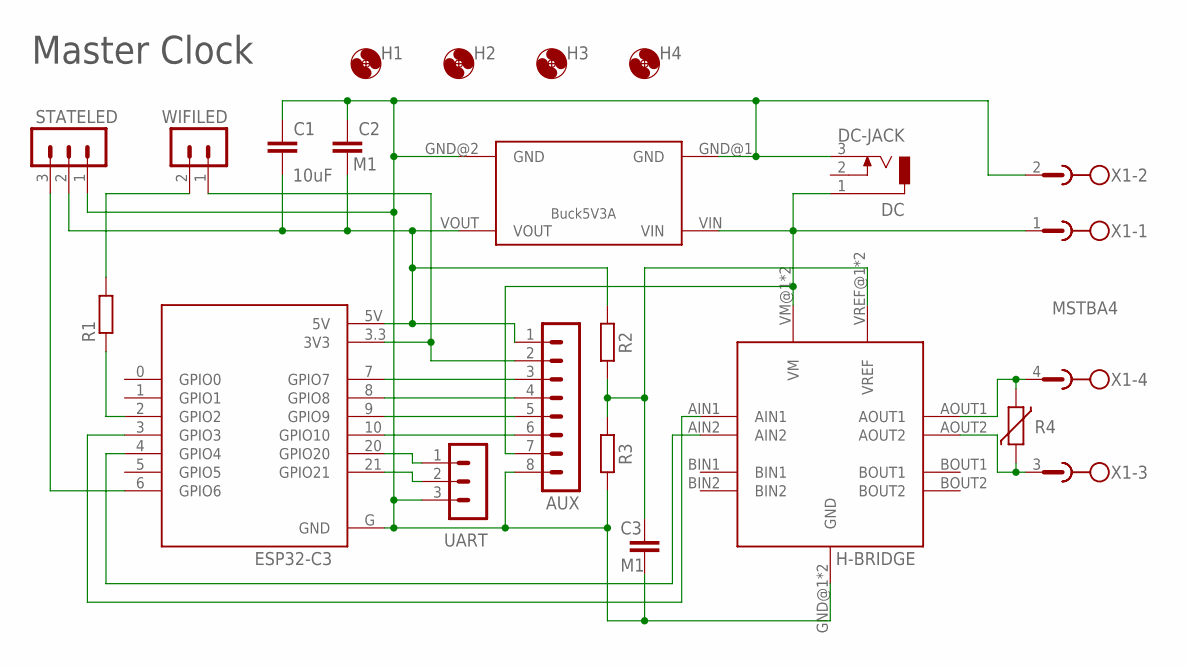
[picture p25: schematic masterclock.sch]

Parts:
AUX: CON-LSTB_MA08-108; CON-LSTB-MA08-1-NS08
C1: 10uF; C1206
C2, C3: M1; C0805
DC: DC-JACK; DCJ0202
ESP32-C3: ESP32-C3_SUPERMINI; ESP32-C3_SUPERMINI_MODULE_ESP32-C3_SUPERMINI
H1, H2, H3, H4: MOUNT-HOLE3,0-2,5; 3,0-2,5
H-BRIDGE: A4950_MODULE
R1, R2, R3: R-EU_R0805; R0805
R4: VARISTORS07KS07K385; S07K385
STATELED: CON-LSTB_MA03-108; CON-LSTB_MA03-1-NS08
U$3: BUCK5V3A
UART: CON-LSTB_MA03-108; CON-LSTB_MA03-1-NS08
WIFILED: CON-LSTB_MA02-1NS08; CON-LSTB_MA02-1-NS08
X1: MSTBA4

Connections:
3V3: AUX.2, ESP32-C3.3.3 (3V3), WIFILED.1
5V: AUX.1, C1.2, C2.2, ESP32-C3.5V, R2.2, STATELED.2, U$3.VOUT
GND: AUX.8, C1.1, C2.1, C3.2, DC.3, ESP32-C3.G (GND), H-BRIDGE.GND@1 (GND), H-BRIDGE.GND@2 (GND), R3.1, STATELED.1, U$3.GND@1 (GND), U$3.GND@2 (GND), UART.3, X1.2
GPIO7: AUX.3, ESP32-C3.7 (GPIO7)
GPIO8: AUX.4, ESP32-C3.8 (GPIO8)
GPIO9: AUX.5, ESP32-C3.9 (GPIO9)
GPIO10: AUX.6, ESP32-C3.10 (GPIO10)
unnamed: ESP32-C3.2 (GPIO2), R1.1
unnamed: ESP32-C3.3 (GPIO3), H-BRIDGE.AIN1
unnamed: ESP32-C3.4 (GPIO4), H-BRIDGE.AIN2
unnamed: ESP32-C3.6 (GPIO6), STATELED.3
unnamed: R1.2, WIFILED.2
OUT1: H-BRIDGE.AOUT1, R4.2, X1.4
OUT2: H-BRIDGE.AOUT2, R4.1, X1.3
RX: ESP32-C3.20 (GPIO20), UART.1
TX: ESP32-C3.21 (GPIO21), UART.2
VIN: AUX.7, DC.1, H-BRIDGE.VM@1 (VM), H-BRIDGE.VM@2 (VM), U$3.VIN, X1.1
VREF: C3.1, H-BRIDGE.VREF@1 (VREF), H-BRIDGE.VREF@2 (VREF), R2.1, R3.2

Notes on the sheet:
Master Clock

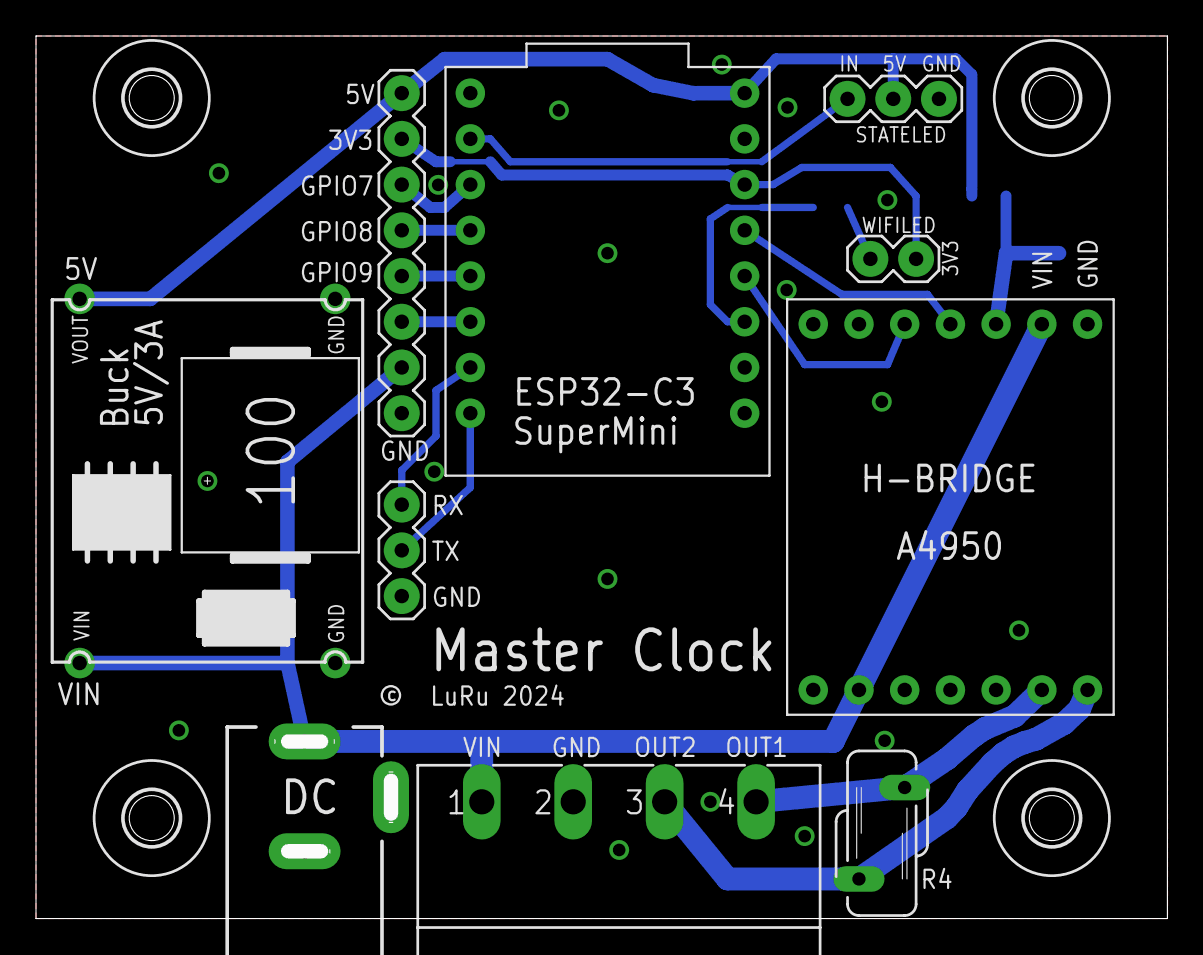
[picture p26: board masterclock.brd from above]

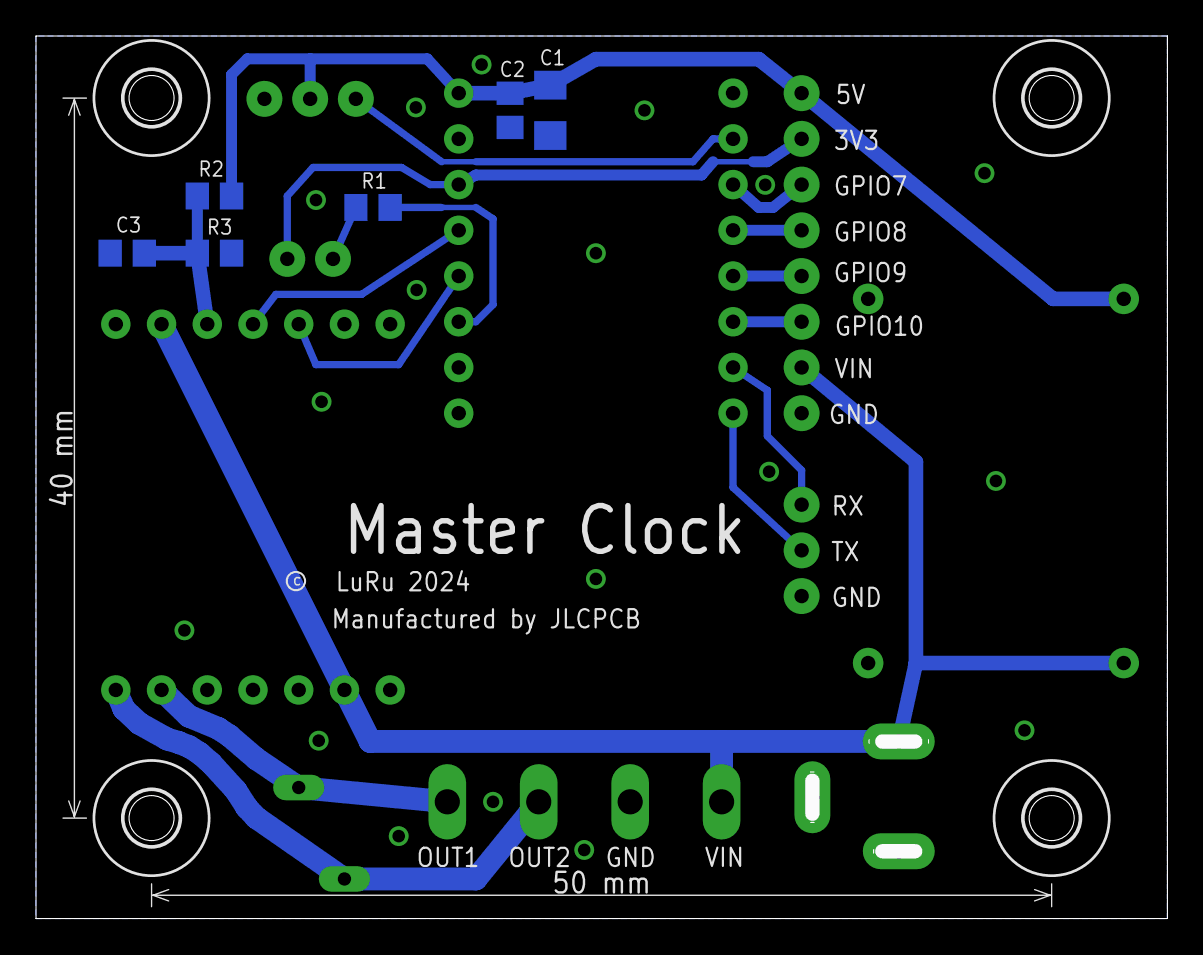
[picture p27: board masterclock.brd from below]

Board: 2 copper layers, 62.9 x 49.0 mm, 20 parts (6 on the bottom side), 18 nets.

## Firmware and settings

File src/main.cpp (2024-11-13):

#define STR(A) #A
#define STRINGIFY(A) STR(A)
const char *http_username = "admin";
#include "Arduino.h"
#include <ArduinoJson.h>
#include "FastLED.h"
#include <WiFi.h>
void WiFiEvent(WiFiEvent_t);
char *cpycharar(char *destination, const char *source, size_t num);

#include <ESPmDNS.h>
#ifdef OTA
#include <Update.h>
#endif
#include <AsyncTCP.h>
#include <ESPAsyncWebServer.h>
#include <LittleFS.h>

struct WLAN
{
  char name[17];
  uint8_t bssid[6] = {0, 0, 0, 0, 0, 0};
  char pass[33];
  char ssid[33];
  uint8_t dhcp;
  IPAddress ipaddress;
  IPAddress subnet;
  IPAddress dnsadd;
  IPAddress gateway;
};
WLAN wlans[8];
uint8_t RESERVEDGPIOS[8];

uint8_t wlannum = 0;
bool shouldReboot = false;
bool formatreq = false;

#ifndef USEWEBH
#include <SPIFFSEditor.h>
#else
//  these are from vendors
#include "webh/glyphicons-halflings-regular.woff.gz.h"
#include "webh/required.css.gz.h"
#include "webh/required.js.gz.h"
// these are from us which can be updated and changed
#include "webh/masterclock.js.gz.h"
#include "webh/masterclock.html.gz.h"
#include "webh/index.html.gz.h"
#endif

#include <time.h>
#include "esp_sntp.h"

#define FSIF true // Format LittleFS if not existing

uint8_t sl_hour = 3;
uint8_t sl_min = 0;
uint8_t sl_hour_old = 3;
uint8_t sl_min_old = 0;
uint8_t odd;
uint8_t oddcounter = 0;
uint8_t evencounter = 0;

enum sl_mode
{
  SL_OFF,
  SL_WAIT,
  SL_ACCC_UP,
  SL_ON,
  SL_EVENVOLT,
  SL_ODDVOLT
};
sl_mode SL_MODE = SL_OFF;
void changeSLmode(sl_mode mode, uint8_t hr, uint8_t mn);
void ChangeStateLed(sl_mode val);

enum mode_wifi
{
  WF_NONE,
  WF_AP,
  WF_APDEF,
  WF_STA,
  WF_WAITSTA
};
mode_wifi WF_MODE = WF_NONE;

const uint8_t blickwaitsta[2] = {1, 9};
const uint8_t blickap[4] = {1, 1, 1, 7};
const uint8_t blickapdef[6] = {1, 1, 1, 1, 1, 5};
uint8_t blickstate = 0;
uint8_t blickcount = 0;
bool wifiledstate = 1;
bool WIFILEDON = 0;

bool STAmode = true;
bool APstart = false;
bool gotIP = false;
bool clockReq = false;
bool reconnect = false;
bool rcnnct = false;
bool scanfinished = false;
uint8_t scanmode = 0;

int16_t nets;

AsyncWebServer server(80);
AsyncWebSocket weso("/ws");
uint8_t messageid = 0;

CRGB stateled[1];

#include "config.h"
Config config;
#include "loadConfig.h"
#include "wsResponses.h"
#include "websocket.h"
#include "webserver.h"

#include "esp_log.h"

const char *TAG = "main"; // For debug lines
char timetxt[9];          // Converted timeinfo
bool time_req = false;    // Set time requested
bool min_req = false;     // Set minute requested
bool checkwait_req = false;
bool accc_up_req = false;

int16_t accc_up_counter = 0;
uint8_t accc_up_imp_counter = 0;
uint8_t accc_up_gap_counter = 0;

struct tm timeinfo; // Will be filled by NTP server
time_t now;
struct tm timfo;
bool tim5s_req = false;
int8_t count5sec = 0; // Counter for activate 5 seconds process;
time_t now2;
time_t old = 0;

hw_timer_t *timer = NULL; // For timer

// the number "num" must be at least "1" smaller than the size of the array "destination" !!!
char *cpycharar(char *destination, const char *source, size_t num)
{
  destination[0] = '\0';
  return strncat(destination, source, num);
}

void gettime()
{
  time(&now);                        // read the current time
  localtime_r(&now, &timfo);         // update the structure timfo with the current time
  sprintf(timetxt, "%02d:%02d:%02d", // Format new time to a string
          timfo.tm_hour,
          timfo.tm_min,
          timfo.tm_sec);
}

//**************************************************************************************************
//                                     D I V M O D 6 0                                             *
//**************************************************************************************************
// Fast routine that provides both / 60 and % 60 for integer math                                  *
// This is an part of Rob Tillaart's excellent fast_math library                                   *
// https://github.com/RobTillaart/fast_math                                                        *
//**************************************************************************************************
void divmod60(uint32_t in, uint8_t *odd_, uint8_t *mod)
{
  uint32_t q = (in >> 1) + (in >> 5);
  q = (q + (q >> 8) + (q >> 16) + (q >> 24)) >> 5;
  uint8_t r = in - q * 60;
  if (r > 59)
  {
    q++;
    r -= 60;
  };
  *odd_ = q & 1;
  *mod = r;
}

//**************************************************************************************************
//                                     D I V M O D 3 0                                             *
//**************************************************************************************************
// Fast routine that provides both / 30 and % 30 for integer math                                  *
// This is derived from the divmod60 routine                                                       *
//**************************************************************************************************
void divmod30(uint32_t in, uint8_t *odd_, uint8_t *mod)
{
  uint32_t q = in + (in >> 4);
  q = (q + (q >> 8) + (q >> 16) + (q >> 24)) >> 5;
  uint8_t r = in - q * 30;
  if (r > 29)
  {
    q++;
    r -= 30;
  };
  *odd_ = q & 1;
  *mod = r;
}

//**************************************************************************************************
//                                          T I M E R 1 0 0                                        *
//**************************************************************************************************
// Called every 100 msec on interrupt level, so must be in IRAM and no lengthy operations          *
// allowed.                                                                                        *
//**************************************************************************************************
void IRAM_ATTR timer100()
{
  uint8_t m;
  time(&now2);          // read the current time [sec]
  bool wholemin = true; // for linetype == 60 sec each pulse means a whole minute
  if (now2 != old)      // new second just started ?
  {
    old = now2;
    time_req = true;
    if (config.linetype == 60)
    {
      divmod60(old, &odd, &m);
    } // has a new minute just started?
    else
    {
      divmod30(old, &odd, &m);
    } // has a new half-minute just started?
    if (!m) // if yes ...
    {
      if (SL_MODE == SL_ON) // and at the same time the SL state is ON
      {
        if (odd)
        {
          oddcounter = config.plength;
          digitalWrite(config.oddpin, HIGH);
          if (config.linetype == 30)
          {
            wholemin = false;
          } // if a half-minute is odd, then it is ONLY a half-minute and not a full minute
        }
        else
        {
          evencounter = config.plength;
          digitalWrite(config.evenpin, HIGH);
        }
        if (wholemin)
        {
          if (++sl_min == 60)
          {
            sl_min = 0;
            if (++sl_hour == config.cycle)
            {
              sl_hour = 0;
            }
          }
          min_req = true;
        }
      }
      else if (SL_MODE == SL_WAIT)
      {
        checkwait_req = true;
      }
    }
  }

  if (SL_MODE == SL_ACCC_UP)
  {
    if (!accc_up_req)
    {
      if (accc_up_imp_counter > 0)
      {
        if (--accc_up_imp_counter == 0)
        {
          if (sl_min & 1)
          {
            digitalWrite(config.evenpin, LOW); // end impuls
          }
          else
          {
            digitalWrite(config.oddpin, LOW); // end impuls
          }
          accc_up_gap_counter = config.glength;
          if (wholemin)
          {
            if (++sl_min == 60)
            {
              sl_min = 0;
              if (++sl_hour == config.cycle)
              {
                sl_hour = 0;
              }
            }
            if (--accc_up_counter == 0)
            {
              accc_up_gap_counter = 0;
              accc_up_imp_counter = 0;
              accc_up_req = true;
            }
          }
        }
      }
      else if (accc_up_gap_counter > 0)
      {
        if (--accc_up_gap_counter == 0)
        {
          if (sl_min & 1)
          {
            digitalWrite(config.evenpin, HIGH); // start impuls
          }
          else
          {
            digitalWrite(config.oddpin, HIGH); // start impuls
          }
          accc_up_imp_counter = config.plength;
        }
      }
      else if (accc_up_imp_counter == 0 && accc_up_gap_counter == 0) // start of ACC mode
      {
        if (sl_min & 1)
        {
          digitalWrite(config.evenpin, HIGH); // start impuls
        }
        else
        {
          digitalWrite(config.oddpin, HIGH); // start impuls
        }
        accc_up_imp_counter = config.plength;
      }
    }
  }
  else if (SL_MODE == SL_ON)
  {
    if (oddcounter > 0)
    {
      if (--oddcounter == 0)
      {
        digitalWrite(config.oddpin, LOW); // end impuls
      }
    }
    else if (evencounter > 0)
    {
      if (--evencounter == 0)
      {
        digitalWrite(config.evenpin, LOW); // end impuls
      }
    }
  }

  switch (WF_MODE)
  {
  case WF_WAITSTA:
    if (++blickcount >= blickwaitsta[blickstate])
    {
      blickcount = 0;
      if (++blickstate >= 2)
      {
        blickstate = 0;
      }
      wifiledstate = !wifiledstate; // invert LED
      digitalWrite(config.wifipin, wifiledstate);
    }
    break;
  case WF_AP:
    if (++blickcount >= blickap[blickstate])
    {
      blickcount = 0;
      if (++blickstate >= 4)
      {
        blickstate = 0;
      }
      wifiledstate = !wifiledstate; // invert LED
      digitalWrite(config.wifipin, wifiledstate);
    }
    break;
  case WF_APDEF:
    if (++blickcount >= blickapdef[blickstate])
    {
      blickcount = 0;
      if (++blickstate >= 6)
      {
        blickstate = 0;
      }
      wifiledstate = !wifiledstate; // invert LED
      digitalWrite(config.wifipin, wifiledstate);
    }
    break;
  default:
    break;
  }
  if (++count5sec == 50) // 5 seconds passed?
  {
    tim5s_req = true; // Yes, do 5 second procedure
    count5sec = 0;    // Reset count
  }
}

bool compareBSSID(const uint8_t *val1, uint8_t val2[6])
{
  for (byte i = 0; i < 6; i++)
  {
    if (*(val1 + i) != val2[i])
    {
      return false;
    }
  }
  return true;
}

bool isZero(uint8_t arr[6])
{
  for (uint8_t i = 0; i < 6; i++)
  {
    if (arr[i] != 0)
    {
      return false;
    }
  }
  return true;
}

// Callback function (gets called when time adjusts via NTP)
void timeavailable(struct timeval *t)
{
  ESP_LOGW(TAG, "Got time adjustment from NTP!");
  // how to get time info:
  time(&now);
  localtime_r(&now, &timfo);
  char timeStringBuff[50]; // 50 chars should be enough
  strftime(timeStringBuff, sizeof(timeStringBuff), "%A, %B %d %Y %H:%M:%S", &timfo);
  ESP_LOGW(TAG, "%s", timeStringBuff);
}

void ChangeStateLed(sl_mode val)
{
  switch (val)
  {
  case SL_OFF:
    stateled[0] = CRGB(201, 0, 0); // Red
    break;
  case SL_WAIT:
    stateled[0] = CRGB(128, 0, 128); // Purple
    break;
  case SL_ACCC_UP:
    stateled[0] = CRGB(0, 56, 255); // Blue
    break;
  case SL_ON:
    stateled[0] = CRGB(50, 174, 0); // Green
    break;
  case SL_EVENVOLT:
    stateled[0] = CRGB(255, 215, 0); // Gold
    break;
  case SL_ODDVOLT:
    stateled[0] = CRGB(255, 144, 144); // Pink
    break;
  default:
    stateled[0] = CRGB::Black;
    break;
  }
  FastLED[0].showLeds(config.brghtnss);
}

void changeSLmode(sl_mode mode, uint8_t hr, uint8_t mn)
{
  if (mode == SL_MODE)
  {
    return;
  }
  switch (mode)
  {
  case SL_OFF:
    digitalWrite(config.oddpin, LOW);
    digitalWrite(config.evenpin, LOW);
    SL_MODE = mode;
    break;
  case SL_WAIT:
    SL_MODE = SL_OFF;
    digitalWrite(config.oddpin, LOW);
    digitalWrite(config.evenpin, LOW);
    sl_hour = hr;
    sl_min = mn;
    SL_MODE = mode;
    break;
  case SL_ACCC_UP:
    SL_MODE = SL_OFF;
    digitalWrite(config.oddpin, LOW);
    digitalWrite(config.evenpin, LOW);
    sl_hour = hr;
    sl_min = mn;
    accc_up_req = true;
    accc_up_gap_counter = 0;
    accc_up_imp_counter = 0;
    break;
  case SL_ON:
    digitalWrite(config.oddpin, LOW);
    digitalWrite(config.evenpin, LOW);
    SL_MODE = SL_OFF;
    sl_hour = hr;
    sl_min = mn;
    SL_MODE = mode;
    break;
  case SL_EVENVOLT:
    SL_MODE = SL_OFF;
    digitalWrite(config.oddpin, LOW);
    digitalWrite(config.evenpin, HIGH);
    sl_hour = hr;
    sl_min = mn;
    SL_MODE = mode;
    break;
  case SL_ODDVOLT:
    SL_MODE = SL_OFF;
    digitalWrite(config.evenpin, LOW);
    digitalWrite(config.oddpin, HIGH);
    sl_hour = hr;
    sl_min = mn;
    SL_MODE = mode;
    break;
  default:
    break;
  }
  ChangeStateLed(SL_MODE);
}

void findWifi(bool async)
{
  IPAddress zeroaddr(0, 0, 0, 0);
  WiFi.config(zeroaddr, zeroaddr, zeroaddr); // reset static addres (issue reconnect from static to DHCP)
  WiFi.disconnect(true, true);
  WiFi.persistent(false);
  WiFi.mode(WIFI_OFF);
  WiFi.mode(WIFI_STA);
  WiFi.setHostname(config.hostnm); // define hostname
  scanmode = (uint8_t)async;
  WiFi.scanNetworks(async, true); // async, show hidden
}
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
void loop()
{
  char shorttimetxt[6];
  char sub[3];
  uint32_t now_;
  uint8_t ix;
  uint8_t r_h;
  uint16_t sl_m;
  uint16_t r_m;

  if (time_req)
  {
    if (weso.count())
    {
      sendTime(NULL);
    }
    time_req = false;
    if (min_req)
    {
      if (weso.count())
      {
        sendImpuls(NULL);
      }
      // check if the times match (it won't e.g. when DST starts or ends)
      gettime();
      r_h = timfo.tm_hour;
      r_h = (r_h >= config.cycle) ? r_h - config.cycle : r_h;
      sl_m = sl_min + 60 * sl_hour;
      r_m = timfo.tm_min + 60 * r_h;
      int16_t diff_m = r_m - sl_m;
      if (diff_m > 0) // slave clock is behind
      {
        changeSLmode(SL_ACCC_UP, sl_hour, sl_min);
      }
      else if (diff_m < 0) // slave clock is ahead
      {
        changeSLmode(SL_WAIT, sl_hour, sl_min);
        if (weso.count())
        {
          sendSlaveMode(NULL);
        }
      }
      min_req = false;
    }
  }
  if (checkwait_req)
  {
    gettime();
    r_h = timfo.tm_hour;
    r_h = (r_h >= config.cycle) ? r_h - config.cycle : r_h;
    if (r_h == sl_hour && timfo.tm_min == sl_min)
    {
      SL_MODE = SL_ON;
      ChangeStateLed(SL_MODE);
      sendSlaveMode(NULL);
    }
    checkwait_req = false;
  }
  if (accc_up_req)
  {
    uint8_t corr = 0;
    gettime();
    r_h = timfo.tm_hour;
    r_h = (r_h >= config.cycle) ? r_h - config.cycle : r_h;
    sl_m = sl_min + 60 * sl_hour;
    r_m = timfo.tm_min + 60 * r_h;
    accc_up_counter = r_m - sl_m;
    if (accc_up_counter == 0)
    {
      SL_MODE = SL_ON;
      ChangeStateLed(SL_MODE);
      sendSlaveMode(NULL);
    }
    else if ((accc_up_counter < 0) && (accc_up_counter > -5))
    {
      SL_MODE = SL_WAIT;
      ChangeStateLed(SL_MODE);
      sendSlaveMode(NULL);
    }
    else if (accc_up_counter < 0)
    {
      uint16_t impcycle = 1 + config.cycle * 60 * (60 / config.linetype);
      accc_up_counter += impcycle;
      if (SL_MODE != SL_ACCC_UP)
      {
        SL_MODE = SL_ACCC_UP;
        ChangeStateLed(SL_MODE);
        sl_hour_old = sl_hour;
        sl_min_old = sl_min;
        sendSlaveMode(NULL);
      }
    }
    else if (accc_up_counter > 0)
    {
      accc_up_counter += 1;
      if (SL_MODE != SL_ACCC_UP)
      {
        SL_MODE = SL_ACCC_UP;
        ChangeStateLed(SL_MODE);
        sl_hour_old = sl_hour;
        sl_min_old = sl_min;
        sendSlaveMode(NULL);
      }
    }
    accc_up_req = false;
  }

  if (SL_MODE == SL_ACCC_UP)
  {
    if ((sl_hour != sl_hour_old) || (sl_min != sl_min_old))
    {
      sendImpuls(NULL);
    }
    sl_hour_old = sl_hour;
    sl_min_old = sl_min;
  }

  if (tim5s_req)
  {
    if (weso.count())
    {
      weso.cleanupClients();
      sendHeartBeat(NULL);
    }
    tim5s_req = false;
  }

  if (WF_MODE == WF_WAITSTA)
  {
    if (!rcnnct)
    {
      scanfinished = false;
      findWifi(true); // async
      rcnnct = true;
    }
    else
    {
      if (scanfinished)
      {
        if (!wifiFound())
        {
          rcnnct = false;
        }
        scanfinished = false;
      }
    }
  }

  if (gotIP)
  {
    WF_MODE = WF_STA;
    blickstate = 0;
    blickcount = 0;
    wifiledstate = WIFILEDON; // lit
    digitalWrite(config.wifipin, wifiledstate);
    if (reconnect)
    {
      vTaskDelay(8000 / portTICK_PERIOD_MS);
      reconnect = false;
    }
    else
    {
      vTaskDelay(4000 / portTICK_PERIOD_MS);
    }
    char bufIP[16];
    IPAddress ip = WiFi.localIP();
    sprintf(bufIP, "%d.%d.%d.%d", ip[0], ip[1], ip[2], ip[3]);
    ESP_LOGW(TAG, "Local IP Address: %s", bufIP);
    gotIP = false;
  }
  if (APstart)
  {
    char bufIP[16];
    IPAddress ip = WiFi.softAPIP();
    sprintf(bufIP, "%d.%d.%d.%d", ip[0], ip[1], ip[2], ip[3]);
    ESP_LOGW(TAG, "AP IP Address: %s", bufIP);
    APstart = false;
  }

  if (shouldReboot)
  {
    ESP_LOGW(TAG, "System is going to reboot ...");
    vTaskDelay(1000 / portTICK_PERIOD_MS);
    ESP.restart();
  }
  if (formatreq)
  {
    shouldReboot = true;
    ESP_LOGW(TAG, "Factory reset initiated ...");
    File cfgjson = LittleFS.open("/config.json", FILE_READ);
    if (cfgjson) // Open success?
    {
      cfgjson.close(); // Yes, close file
      LittleFS.remove("/config.json");
    }
    vTaskDelay(1000 / portTICK_PERIOD_MS);
    ESP.restart();
  }
}
//=======================================================================

void WiFiEvent(WiFiEvent_t event)
{
  char s[35];
  switch (event)
  {
  case SYSTEM_EVENT_WIFI_READY:
    cpycharar(s, "SYSTEM_EVENT_WIFI_READY", 34);
    break;

  case ARDUINO_EVENT_WIFI_SCAN_DONE:
    cpycharar(s, "ARDUINO_EVENT_WIFI_SCAN_DONE", 34);
    if (scanmode == 1)
    {
      nets = WiFi.scanComplete();
      scanfinished = true;
      ESP_LOGW(TAG, "Scan complete. Number of networks found: %d", nets);
    }
    else if (scanmode == 2)
    {
      nets = WiFi.scanComplete();
      sendScanResult(nets, NULL);
    }
    break;

  case SYSTEM_EVENT_STA_START:
    cpycharar(s, "SYSTEM_EVENT_STA_START", 34);
    break;

  case SYSTEM_EVENT_STA_STOP:
    cpycharar(s, "SYSTEM_EVENT_STA_STOP", 34);
    break;

  case SYSTEM_EVENT_STA_CONNECTED:
    STAmode = true;
    cpycharar(s, "SYSTEM_EVENT_STA_CONNECTED", 34);
    break;

  case SYSTEM_EVENT_STA_DISCONNECTED:
    if (WF_MODE != WF_WAITSTA)
    {
      reconnect = true;
      rcnnct = false;
      WF_MODE = WF_WAITSTA;
      blickstate = 0;
      wifiledstate = WIFILEDON;
    }
    cpycharar(s, "SYSTEM_EVENT_STA_DISCONNECTED", 34);
    break;

  case SYSTEM_EVENT_STA_AUTHMODE_CHANGE:
    cpycharar(s, "SYSTEM_EVENT_STA_AUTHMODE_CHANGE", 34);
    break;

  case SYSTEM_EVENT_STA_GOT_IP:
    gotIP = true;
    cpycharar(s, "SYSTEM_EVENT_STA_GOT_IP", 34);
    break;

  case SYSTEM_EVENT_STA_LOST_IP:
    cpycharar(s, "SYSTEM_EVENT_STA_LOST_IP", 34);
    break;

  case SYSTEM_EVENT_STA_WPS_ER_SUCCESS:
    cpycharar(s, "SYSTEM_EVENT_STA_WPS_ER_SUCCESS", 34);
    break;

  case SYSTEM_EVENT_STA_WPS_ER_FAILED:
    cpycharar(s, "SYSTEM_EVENT_STA_WPS_ER_FAILED", 34);
    break;

  case SYSTEM_EVENT_STA_WPS_ER_TIMEOUT:
    cpycharar(s, "SYSTEM_EVENT_STA_WPS_ER_TIMEOUT", 34);
    break;

  case SYSTEM_EVENT_STA_WPS_ER_PIN:
    cpycharar(s, "SYSTEM_EVENT_STA_WPS_ER_PIN", 34);
    break;

  case SYSTEM_EVENT_AP_START:
    cpycharar(s, "SYSTEM_EVENT_AP_START", 34);
    break;

  case SYSTEM_EVENT_AP_STOP:
    cpycharar(s, "SYSTEM_EVENT_AP_STOP", 34);
    break;

  case SYSTEM_EVENT_AP_STACONNECTED:
    cpycharar(s, "SYSTEM_EVENT_AP_STACONNECTED", 34);
    break;

  case SYSTEM_EVENT_AP_STADISCONNECTED:
    cpycharar(s, "SYSTEM_EVENT_AP_STADISCONNECTED", 34);
    break;

  case SYSTEM_EVENT_AP_STAIPASSIGNED:
    cpycharar(s, "SYSTEM_EVENT_AP_STAIPASSIGNED", 34);
    break;

  case SYSTEM_EVENT_AP_PROBEREQRECVED:
    cpycharar(s, "SYSTEM_EVENT_AP_PROBEREQRECVED", 34);
    break;

  case SYSTEM_EVENT_GOT_IP6:
    cpycharar(s, "SYSTEM_EVENT_GOT_IP6", 34);
    break;

  case SYSTEM_EVENT_ETH_START:
    cpycharar(s, "SYSTEM_EVENT_ETH_START", 34);
    break;

  case SYSTEM_EVENT_ETH_STOP:
    cpycharar(s, "SYSTEM_EVENT_ETH_STOP", 34);
    break;

  case SYSTEM_EVENT_ETH_CONNECTED:
    cpycharar(s, "SYSTEM_EVENT_ETH_CONNECTED", 34);
    break;

  case SYSTEM_EVENT_ETH_DISCONNECTED:
    cpycharar(s, "SYSTEM_EVENT_ETH_DISCONNECTED", 34);
    break;

  case SYSTEM_EVENT_ETH_GOT_IP:
    cpycharar(s, "SYSTEM_EVENT_ETH_GOT_IP", 34);
    break;

  default:
    cpycharar(s, "[ UNKNOWN ]", 34);
    break;

  } // switch
  ESP_LOGW(TAG, "WiFi-event: >>>%s<<<", s);
} // WiFiEvent

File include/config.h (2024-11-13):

struct Config {
	uint8_t evenpin = 3;
	uint8_t oddpin = 4;
	uint8_t wifipin = 2;
	//uint8_t rgbpin = 6;
	uint8_t brghtnss = 16;
	uint8_t wifiledon = 0;
	uint16_t linetype = 60;
	uint8_t cycle = 12;
	uint8_t plength = 8;
	uint8_t glength = 2;
    char http_pass[24] = "admin";
    char hostnm[24] = "ESP32_MasterClock";
    char ntpServer[24] = "pool.ntp.org";
	int ntpInterval = 15;
    char timeZone[40] = "CET-1CEST,M3.5.0,M10.5.0/3";
    char tzname[24] = "Europe/Prague";
    char dateformat[11] = "dd-mm-yyyy";
    IPAddress apaddress = {192, 168, 4, 1}; 
    IPAddress apsubnet = {255, 255, 255, 0}; 
    char apssid[33] = "ESP32_MasterClock";
};

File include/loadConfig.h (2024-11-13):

const char *LCTAG = "loadConfig"; // For debug lines
#include "base64.hpp"

void decodeB64(const char *inputStr, char *output)
{
	unsigned char ibuff[65];
	memcpy(ibuff, inputStr, 65);
	unsigned char obuff[33];
	unsigned int string_length = decode_base64(ibuff, obuff);
	obuff[string_length] = '\0';
	memcpy(output, obuff, string_length + 1);
}

bool ICACHE_FLASH_ATTR loadConfiguration(Config &config)
{
	uint8_t resix = 0;
	RESERVEDGPIOS[resix++] = 6; // default RGB LED pin
	File configFile = LittleFS.open("/config.json", "r");
	if (!configFile)
	{
#ifdef DEBUG
		ESP_LOGW(LCTAG, "Failed to open config file");
#endif
		pinMode(config.wifipin, OUTPUT);
		digitalWrite(config.wifipin, HIGH);
		return false;
	}
	size_t size = configFile.size();
	std::unique_ptr<char[]> buf(new char[size]);
	configFile.readBytes(buf.get(), size);
	JsonDocument json;
	auto error = deserializeJson(json, buf.get());
	if (error)
	{
#ifdef DEBUG
		ESP_LOGW(LCTAG, "Failed to parse config file");
#endif
		pinMode(config.wifipin, OUTPUT);
		digitalWrite(config.wifipin, HIGH);
		return false;
	}
#ifdef DEBUG
	ESP_LOGW(LCTAG, "Config file found");
#endif

	JsonObject hardware = json["hardware"];
	JsonObject clock = json["clock"];
	JsonObject general = json["general"];
	JsonObject ntp = json["ntp"];
	JsonArray networks = json["network"]["networks"];

	WIFILEDON = (hardware.containsKey("wifiledon")) ? hardware["wifiledon"] : 0;

	if (hardware.containsKey("evenpin"))
	{
		config.evenpin = hardware["evenpin"];
		if (config.evenpin != 255)
		{
			pinMode(config.evenpin, OUTPUT);
			digitalWrite(config.evenpin, LOW);
		}
	}
	if (hardware.containsKey("oddpin"))
	{
		config.oddpin = hardware["oddpin"];
		if (config.oddpin != 255)
		{
			pinMode(config.oddpin, OUTPUT);
			digitalWrite(config.oddpin, LOW);
		}
	}

	if (hardware.containsKey("brghtnss"))
	{
       config.brghtnss = hardware["brghtnss"];
	}

	if (hardware.containsKey("wifipin"))
	{
		config.wifipin = hardware["wifipin"];
		if (config.wifipin != 255)
		{
			pinMode(config.wifipin, OUTPUT);
			digitalWrite(config.wifipin, !WIFILEDON);
		}
	}

	wlannum = 0;
	for (JsonObject value : networks)
	{
		cpycharar(wlans[wlannum].name, value["location"].as<const char *>(), 16);
		cpycharar(wlans[wlannum].ssid, value["ssid"].as<const char *>(), 32);
		decodeB64(value["wifipass"].as<const char *>(), wlans[wlannum].pass);
		char bssid[18];
		cpycharar(bssid, value["wifibssid"].as<const char *>(), 17);
		wlans[wlannum].dhcp = value["dhcp"].as<uint8_t>();

		if (strlen(bssid) == 17)
		{
			sscanf(bssid, "%2hhx:%2hhx:%2hhx:%2hhx:%2hhx:%2hhx",
				   &wlans[wlannum].bssid[0], &wlans[wlannum].bssid[1],
				   &wlans[wlannum].bssid[2], &wlans[wlannum].bssid[3],
				   &wlans[wlannum].bssid[4], &wlans[wlannum].bssid[5]);
		}
		if (wlans[wlannum].dhcp == 0)
		{
			wlans[wlannum].ipaddress.fromString(value["ipaddress"].as<const char *>());
			wlans[wlannum].subnet.fromString(value["subnet"].as<const char *>());
			wlans[wlannum].dnsadd.fromString(value["dnsadd"].as<const char *>());
			wlans[wlannum].gateway.fromString(value["gateway"].as<const char *>());
		}
		wlannum++;
	}
	ESP_LOGW(LCTAG, "Number of wlans: %3d", wlannum);

	config.linetype = clock["linetype"].as<uint8_t>();
	config.cycle = clock["cycle"].as<uint8_t>();
	config.plength = clock["plength"].as<uint8_t>();
	config.glength = clock["glength"].as<uint8_t>();
	config.ntpInterval = ntp["interval"].as<int>();
	cpycharar(config.timeZone, ntp["timezone"].as<const char *>(), 39);
	cpycharar(config.tzname, ntp["tzname"].as<const char *>(), 23);
	cpycharar(config.ntpServer, ntp["server"].as<const char *>(), 23);
	cpycharar(config.hostnm, general["hostnm"].as<const char *>(), 23);
	decodeB64(general["psswd"].as<const char *>(), config.http_pass);
	cpycharar(config.apssid, json["network"]["apssid"].as<const char *>(), 32);
	config.apaddress.fromString(json["network"]["apaddress"].as<const char *>());
	config.apsubnet.fromString(json["network"]["apsubnet"].as<const char *>());

	ESP_LOGW(LCTAG, "Configuration done");
	configFile.close();
	return true;
}

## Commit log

2024-11-13 initial project version
    [default.csv, masterclock.brd, masterclock.sch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]
2024-11-14 removing old gerber files
